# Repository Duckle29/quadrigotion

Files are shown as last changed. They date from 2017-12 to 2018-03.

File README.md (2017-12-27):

Quadrigotion: Multiple Motor Drivers, two connectors
============================================================

Often it is useful to have all the motor drivers needed for a machine
on a separate circuit board to be able to mount it to a heatsink or close
to the action. This is what this project is about.
The name **Quadrigotion** is a word amalgamated from 'Quadriga' (Four
horses powering a chariot) and 'Motion'.

Motivation for this project to have motor drivers easily replacable and
testable on my various 3D printers and CNC machines. Since I am also
[developing motion control software][BeagleG], I might have an unusual
high demand for this :)

The idea is to have a common connector type, described below, and various
implementations of that concept. The first implementation is using a TMC2660,
which is the 'big brother' of the more well-known TMC2100.

Other implementations are conceivable e.g. with Pololu modules, DRV8825, or
super high current and voltage drivers for heavy CNC machines.
Implementations can be super bare-bone and not use the SPI connection or
could be configured via SPI using a shift-register and digital potentiometers
if the chips can't be configured with SPI directly.
While the first Quadrigotion implementation happens to also have four motor
drivers, this could of course extend in the future.

The Connector
--------------

##TO BE EDITED TO REFLECT USE OF SMOOTHIE GADGETEER PORTS

The digital input is provided with an IDC connector with 16 pins (2x8) or
20 pins (2x10).
It features a SPI bus to send configuration data and also read motor/driver
status (the actual protocol is of implementation-dependent, but they all can
share the same hardware interface).

| Desc | Pin | Pin | Desc
|---:|:---:|:---:|:---
| GND  | 1 | 2 | VCC (3.3V-5V)
| All Motors ~Enable | 3 | 4 | (not connected; reserved for fault-out)
| ~CS (SPI) | 5 | 6 | CLK (SPI)
| MISO (SPI) | 7 | 8 | MOSI (SPI)
| Step #1 | 9 |  10 | Dir #1
| Step #2 |  11 |  12 | Dir #2
| Step #3 |  13 |  14 | Dir #3
| Step #4 |  15 |  16 | Dir #4 -------- END IDC 16 variant
| Step #5 |  17 |  18 | Dir #5
| Step #6 |  19 |  20 | Dir #6 -------- END IDC 20 variant

It is easy to see that extending the driver count would just require a wider
IDC connector; the serial configuration interface can deal with any
number. A 16 pin IDC connector allows for 4 steppers, the next configuration
with 20 pins would allow for six drivers.

A single Enable-pin is provided that affects all drivers. This makes it easy
to wire up that signal directly e.g. for emergency buttons.
If more individual control of each driver is needed, this can be done via
the SPI connection.

The fast signals for each stepper, step and dir, are provided in
a parallel input with two lines per stepper.

A Quadrigotion connector has a single ChipSelect signal; multiple drivers
on each implementation have to share that bus, e.g. by internally being
organized as a shift register that latches when ~CS goes high again.

One pin (pin 4) is not connected yet, but it is reserved for fault detection
output (e.g stalling, overheating or over-current).

In an upcoming project, I'll build a breakout board to work with [BeagleG].

TMC2660 Implementation
----------------------

The first implementation is based on the TMC2660, a feature-rich motor driver
that can drive up to 4A (2.8A RMS). The 40mmx125mm PCB is a four layer board
which duals as heat conductor for cooling. Multiple M2.5 mounting holes allow
to firmly mount it to a heatsink and get even pressure to individual silicone
heatsink pads.
Power is provided via a 4-pin JST VH connector (3.96mm pitch),
circuit protected with an automotive ATC Mini 297 blade fuse.

You find the gerbers in the [fab/](./fab) directory. Board is also
[shared on OshPark]. Cave: since this is the very first version, no
testing has been done yet with a physical board.

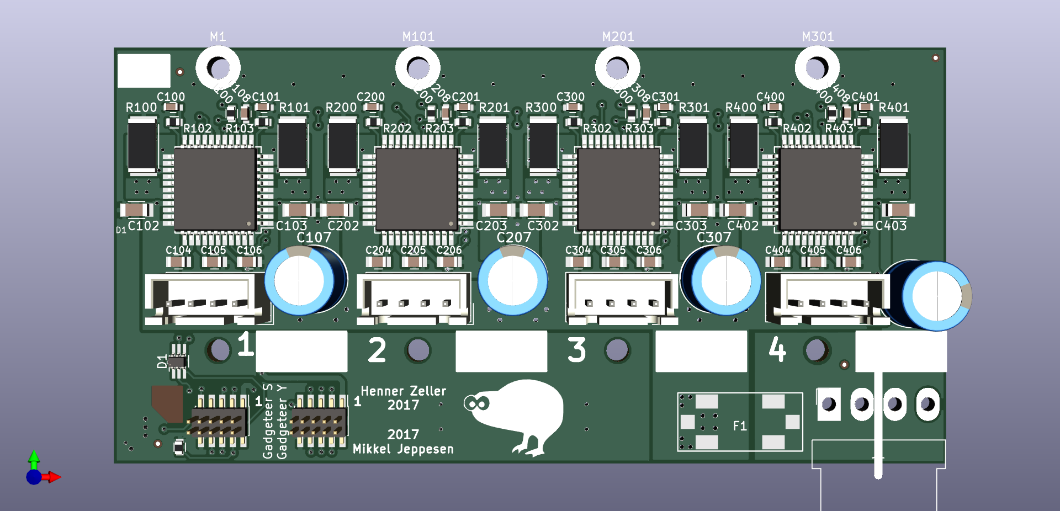
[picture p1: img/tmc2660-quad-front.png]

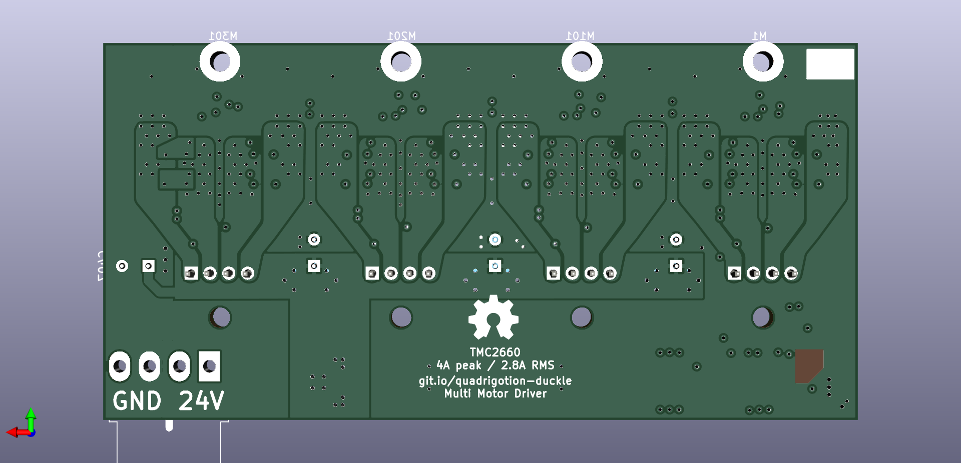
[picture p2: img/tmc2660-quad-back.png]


[BeagleG]: https://github.com/hzeller/beagleg
[shared on OshPark]: https://oshpark.com/shared_projects/M0SQCRdL

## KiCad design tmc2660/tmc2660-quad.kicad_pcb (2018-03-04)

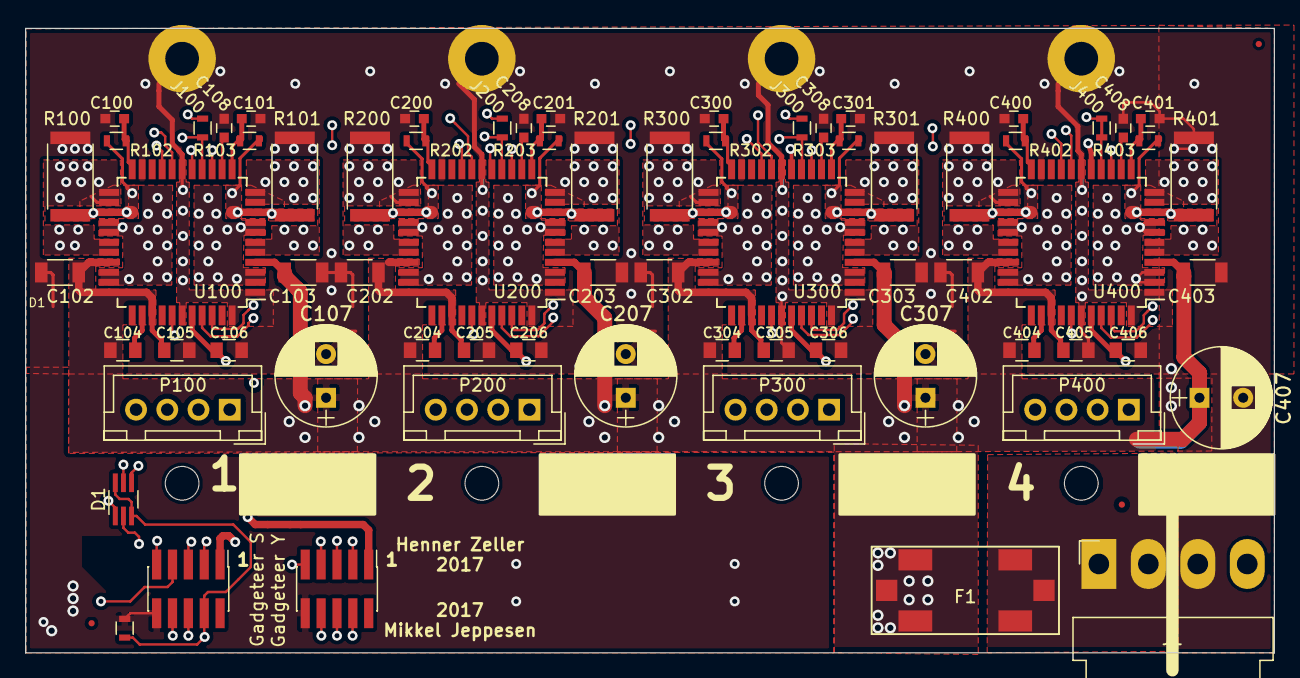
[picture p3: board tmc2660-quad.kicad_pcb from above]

Board: 4 copper layers, 100.0 x 50.0 mm, 78 parts (0 on the bottom side), 65 nets.

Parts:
C100, C101, C200, C201, C300, C301, C400, C401: 10n; C_0603
C102, C103, C202, C203, C302, C303, C402, C403: 10u; C_1206
C104, C105, C106, C204, C205, C206, C304, C305, C306, C404, C405, C406: 100n; C_0805
C107, C207, C307, C407: 180u; CP_Radial_D8.0mm_P3.50mm
C108, C208, C308, C408: 470n; C_0603
D1: BAV70; SOT-363_SC-70-6_Handsoldering
F1: Fuse; BladeFuse-Mini_Keystone-3586
J1: Power; JST_VH_B4PS-VH_2x4x3.96mm_Horizontal
J2: Gadgeteer S; Pin_Header_Straight_2x05_Pitch1.27mm_SMD
J3: 10k; R_0603
J4: Gadgeteer Y; Pin_Header_Straight_2x05_Pitch1.27mm_SMD
J100, J200, J300, J400: 0R; R_0603
M0, M100, M200, M300: Mount; MountingHole_2.7mm_M2.5
M1, M101, M201, M301: Mount; MountingHole_2.7mm_M2.5_Pad
P100, P200, P300, P400: Motor; JST_XH_B04B-XH-A_04x2.50mm_Straight
R100, R101, R200, R201, R300, R301, R400, R401: 0.075; R_2512
R102, R103, R202, R203, R302, R303, R402, R403: 10R; R_0603
U100, U200, U300, U400: TMC2660; LQFP-44_10x10mm_Pitch0.8mm

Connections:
+3V3: C106.1, C206.1, C306.1, C406.1, J2.1, J4.1, U100.40, U200.40, U300.40, U400.40
/PowerIn: F1.2, J1.1, J1.2
/TMC2660-100/A1: P100.2, U100.2, U100.3, U100.7, U100.8
/TMC2660-100/A2: P100.1, U100.5, U100.6, U100.10, U100.11
/TMC2660-100/B1: P100.3, U100.26, U100.27, U100.31, U100.32
/TMC2660-100/B2: P100.4, U100.23, U100.24, U100.28, U100.29
/TMC2660-100/BRA: R101.1, R103.2, U100.9
/TMC2660-100/BRB: R100.1, R102.1, U100.25
/TMC2660-100/STALL: D1.2, U100.38
/TMC2660-100/VHS: C104.2, U100.35
/TMC2660-200/A1: P200.2, U200.2, U200.3, U200.7, U200.8
/TMC2660-200/A2: P200.1, U200.5, U200.6, U200.10, U200.11
/TMC2660-200/B1: P200.3, U200.26, U200.27, U200.31, U200.32
/TMC2660-200/B2: P200.4, U200.23, U200.24, U200.28, U200.29
/TMC2660-200/BRA: R201.1, R203.2, U200.9
/TMC2660-200/BRB: R200.1, R202.1, U200.25
/TMC2660-200/MISO: J100.2, U100.15, U200.14
/TMC2660-200/STALL: D1.1, U200.38
/TMC2660-200/VHS: C204.2, U200.35
/TMC2660-300/A1: P300.2, U300.2, U300.3, U300.7, U300.8
/TMC2660-300/A2: P300.1, U300.5, U300.6, U300.10, U300.11
/TMC2660-300/B1: P300.3, U300.26, U300.27, U300.31, U300.32
/TMC2660-300/B2: P300.4, U300.23, U300.24, U300.28, U300.29
/TMC2660-300/BRA: R301.1, R303.2, U300.9
/TMC2660-300/BRB: R300.1, R302.1, U300.25
/TMC2660-300/MISO: J200.2, U200.15, U300.14
/TMC2660-300/STALL: D1.4, U300.38
/TMC2660-300/VHS: C304.2, U300.35
/TMC2660-400/A1: P400.2, U400.2, U400.3, U400.7, U400.8
/TMC2660-400/A2: P400.1, U400.5, U400.6, U400.10, U400.11
/TMC2660-400/B1: P400.3, U400.26, U400.27, U400.31, U400.32
/TMC2660-400/B2: P400.4, U400.23, U400.24, U400.28, U400.29
/TMC2660-400/BRA: R401.1, R403.2, U400.9
/TMC2660-400/BRB: R400.1, R402.1, U400.25
/TMC2660-400/MISO: J300.2, U300.15, U400.14
/TMC2660-400/STALL: D1.5, U400.38
/TMC2660-400/VHS: C404.2, U400.35
CS: J2.6, U100.18, U200.18, U300.18, U400.18
DIR1: J4.6, U100.41
DIR2: J4.3, U200.41
DIR3: J4.7, U300.41
DIR4: J2.5, U400.41
GLOBAL_MISO: J2.8, U100.14
GLOBAL_MOSI: J2.7, J100.1, J200.1, J300.1, J400.1, J400.2, U400.15
GND: C100.1, C101.2, C102.2, C103.2, C105.2, C106.2, C107.2, C108.2, C200.1, C201.2, C202.2, C203.2, C205.2, C206.2, C207.2, C208.2, C300.1, C301.2, C302.2, C303.2, C305.2, C306.2, C307.2, C308.2, C400.1, C401.2, C402.2, C403.2, C405.2, C406.2, C407.2, C408.2, J1.3, J2.10, J3.2, J4.10, M1.1, M101.1, M201.1, M301.1, R100.2, R101.2, R200.2, R201.2, R300.2, R301.2, R400.2, R401.2, U100.1, U100.17, U100.21, U100.39, U100.44, U200.1, U200.17, U200.21, U200.39, U200.44, U300.1, U300.17, U300.21, U300.39, U300.44, U400.1, U400.17, U400.21, U400.39, U400.44
unnamed: C100.2, R102.2, U100.22
unnamed: C101.1, R103.1, U100.12
unnamed: C108.1, U100.13
unnamed: C200.2, R202.2, U200.22
unnamed: C201.1, R203.1, U200.12
unnamed: C208.1, U200.13
unnamed: C300.2, R302.2, U300.22
unnamed: C301.1, R303.1, U300.12
unnamed: C308.1, U300.13
unnamed: C400.2, R402.2, U400.22
unnamed: C401.1, R403.1, U400.12
unnamed: C408.1, U400.13
SCLK: J2.9, U100.16, U200.16, U300.16, U400.16
STALL: D1.3, D1.6, J2.4, J3.1
STEP1: J4.8, U100.42
STEP2: J4.4, U200.42
STEP3: J4.5, U300.42
STEP4: J4.9, U400.42
VMot: C102.1, C103.1, C104.1, C105.1, C107.1, C202.1, C203.1, C204.1, C205.1, C207.1, C302.1, C303.1, C304.1, C305.1, C307.1, C402.1, C403.1, C404.1, C405.1, C407.1, F1.1, U100.4, U100.30, U100.33, U100.36, U200.4, U200.30, U200.33, U200.36, U300.4, U300.30, U300.33, U300.36, U400.4, U400.30, U400.33, U400.36
~ENABLE: J2.3, U100.19, U200.19, U300.19, U400.19

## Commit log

2017-12-15 Started work on moving to 100x50mm design
    [tmc2660-quad.kicad_pcb]
2017-12-15 Finished squished board
    [tmc2660-block-100.sch, tmc2660-block-200.sch, tmc2660-block-300.sch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]
2017-12-15 Fixed some mistakes pointed out
    [tmc2660-quad.kicad_pcb]
2017-12-15 Fixed break of in1 pour at R300
    [tmc2660-quad.kicad_pcb]
2017-12-15 Further fixed broken gnd pour
    [tmc2660-quad.kicad_pcb]
2017-12-27 Commiting before branching
    [tmc2660-quad.kicad_pcb]
2017-12-27 Initial commit on gadgeteer port version
    [tmc2660-quad.kicad_pcb, tmc2660-quad.sch]
2017-12-27 Added renders
    [tmc2660-quad.kicad_pcb]
2018-03-04 Removed vmot-minipours, uppded BRA/BRB pours priority
    [tmc2660-quad.kicad_pcb]
